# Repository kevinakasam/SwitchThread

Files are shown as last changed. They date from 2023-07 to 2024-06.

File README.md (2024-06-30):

# SwitchThread

The SwitchThread is a smol version of the [Voron Switchwire](https://github.com/VoronDesign/Voron-Switchwire). The goal of this project was/is to keep it in the *rules* of the [Printer for Ants](https://3dprintersforants.com/) - this means 1515 extrusions, a 120mm³ build volume, MGN 7H on all axis, Mini Stealthburner and so on.



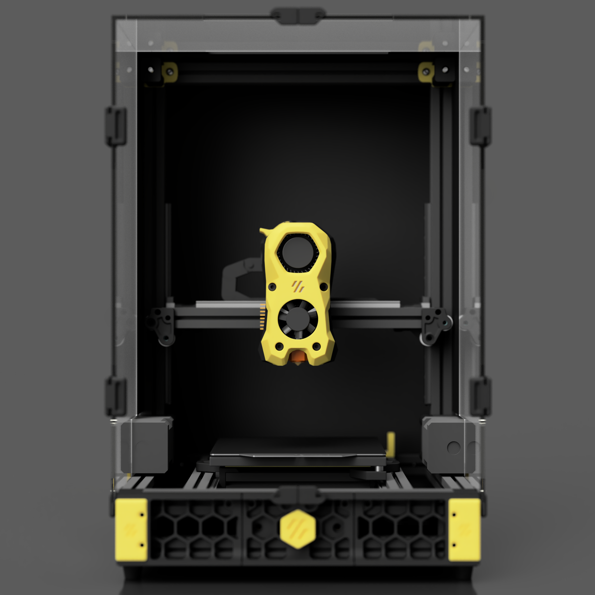
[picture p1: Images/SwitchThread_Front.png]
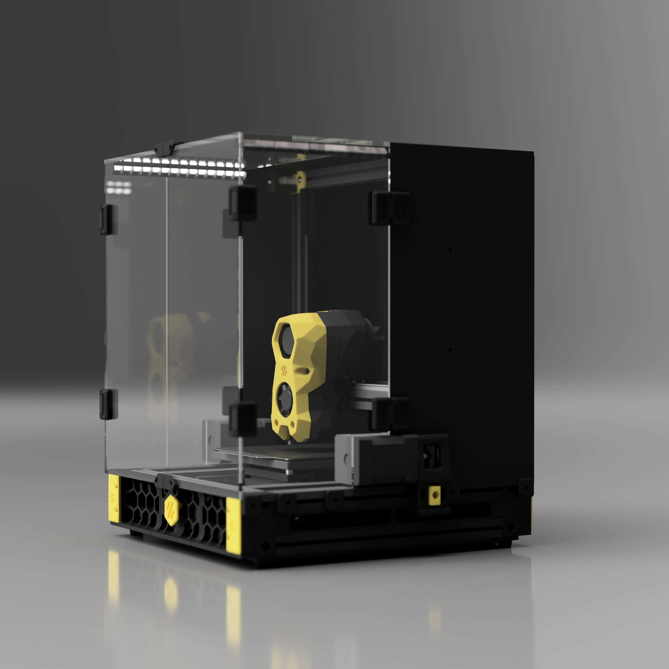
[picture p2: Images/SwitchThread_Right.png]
   

### Beta - Work in progress!

This is a very early work in progress. If you start building, you risk reprinting parts or spending money on hardware that will not be used in the final design. Please take a look at the SwitchThread channel on the [Doomcube Discord](https://discord.gg/doomcube).

The XZ gantry will be getting an update soon. I'm not a fan of the XZ tension mechanism, so I'll be customizing that part. So I would recommend waiting to print the XZ Gantry parts.

### Credits

- The printer is based on the [Voron Switchwire](https://github.com/VoronDesign/Voron-Switchwire) designed by the awesome [Voron Team](https://github.com/VoronDesign). Thanks for making this open source and allow fun projects like this!
- Also many thanks to the [Printer for Ants Team](https://www.3dprintersforants.com/) and Doomcube members for giving me chance to participate to project.
- And very special thanks to Schlongky for pushing me to finally start this project. Thanks for SwitchThreads name, your ideas and all the help with sourcing parts. Also thanks to Oldcrazy and Kyle for jumping on this project even though the CAD wasn't even finished yet!

### See it in action

SwitchThread by myself        |  SwitchThread by SchlongkyDong  
:-------------------------:|:-------------------------:
Serial Request (https://www.reddit.com/r/voroncorexy/comments/16sjrmx/serial_request_switchwire_switchthread_discord/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) | Serial Reques (https://www.reddit.com/r/voroncorexy/comments/16sk4o1/serial_request_switchwire_switchthread_discord/)

### BOM?

The SwitchThread is pretty much a V0 in a different shape, so with a V0 kit you will cover 99% of the parts you need. We're working on a more detailed BOM, but so far you should be fine with a few extra meters of belts and one or two extra pulleys (depending on the Y setup you want to use).

- GT2 Open Belt 6mm: V0 BOM calls for 3 Meters and I used exactly 3 Meters with dual Y, but then you shouldn't misscut
- F623-RS Bearing: V0 BOM calls for 24. You will need 22 with single Y and 28 with dual Y
- Frame: Setting a V0 Frame + a 100mm Tophat Kit as default you get everything you need to build the SwitchThread Frame. The SwitchThread has 300mm long Z extrusions, by deafult you're supposted to join a 200mm extrusion with a 100mm tophat extrusion (two times). Two more 100mm profiles are needed for the bed (so you need 4 100mm extrusions in total, 2 for the bed and 2 to raise z). This beeing said, the following scenarios are possible and should help you to understand what you need:
    - V0 Frame + 100mm Tophat Kit: Join a 200mm extrusion with one of the 100mm tophat extrusions - works perfectly fine with a M3 threaded rod or a headless M3 screw (Take a look [here](https://github.com/zruncho3d/BoxZero#frame))
    - V0 Frame + new 300mm profile: Rather than joining two extrusions together you can also get a new 300mm z extrusion. Probably the easiest way, requires more parts and money though
    - V0 Frame + a saw: If you only have a V0 Frame, you can use a saw to solve this. The SwitchThread will give you 1 spare 200mm profile - you can cut that in half to get the extra 100mm profile (remember you need 4 in total). I would use the cut profile on the bed, simply because it doesn't matter if your cut isn't 100% straight but it does for z.
- Boop: If you want to use Boop, the bed springs are a nogo, I will add a link to nylonspacers once Boop is confirmed.

### Boop and Dual Y

I try to keep this short: You have to decide if you want to use a single or dual Y Motor setup and if you want to use Boop or not. Alternatively you can also use an [ADXL Probe](https://github.com/jniebuhr/adxl345-probe) or any other bed probe - I also want to implement [Klicky](https://github.com/jlas1/Klicky-Probe) + [Sexbolt](https://github.com/VoronDesign/VoronUsers/tree/master/printer_mods/hartk1213/Voron2.4_SexBolt_ZEndstop) to use the [Automatic Z-Calibration](https://github.com/protoloft/klipper_z_calibration#moonraker-updater) macro - I assume we will need a longer x rail for that though, I can't tell right now.

#### Boop

The goal is to support [Boop](https://github.com/PrintersForAnts/Boop) - a mini version of the [Voron Tap](https://github.com/VoronDesign/Voron-Tap/). This hasnt been tested yet but I tried my best to make the Bed as rigid as possible - we will see if that works out. However the decision if you want to use Boop or not is important for the frame build. If you*re going to use boop, you can reuse the counterbore holes in the E-Extrusions of the V0 Frame. If you don't want to use Boop, you will have to drill your own holes.

#### Single / Dual Y

Since we use a 120mm casted bed, there's quite some mass to move around. We had the idea to squeeze to Y motors in there to double the power. This means that you will need an extra Nema 14 stepper (not a driver, you can use the parallel z port on most Mobos) and some extra belts + bearings  (see BOM section above). Also the LRS150 wouldn't fir under the printer - I will find a solution for that.

### ChangeLog

30.06.2024
- Well, finally the first real push of all files. Everything aside panels is working and ready to print :D

28.09.2023
- Mostly bug fixes
- Added missing STLs, everything should be tested now

01.08.2023: XZ Update
- Fixed an issue with the belt path on the right idler
- Added Alternative XZ Tensioners, these will require some different hardware, main difference is a M3x40mm screw and a F623 bearing per side

28.07.2023: Initial Upload

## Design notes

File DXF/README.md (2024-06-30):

Panels are still in the dev. Please use the CAD to take a look at the current state. Aside the Mid panels, everything should fit. Please ping me on Discord before buying any panels.

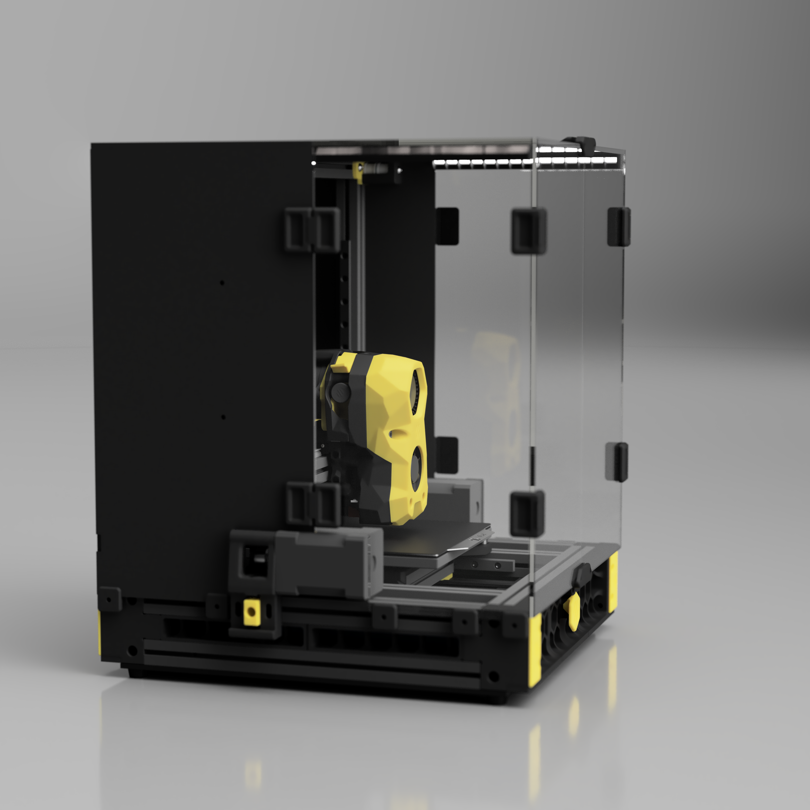
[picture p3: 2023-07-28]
Images/SwitchThread_Left.png

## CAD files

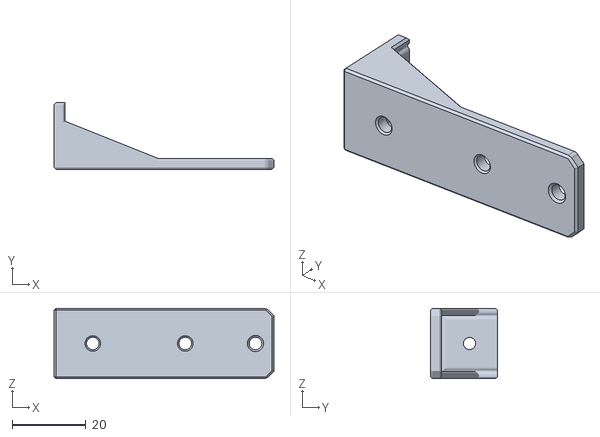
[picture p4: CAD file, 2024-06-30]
STLs/DrillGuide.stl
59.5 x 18.0 x 19.0

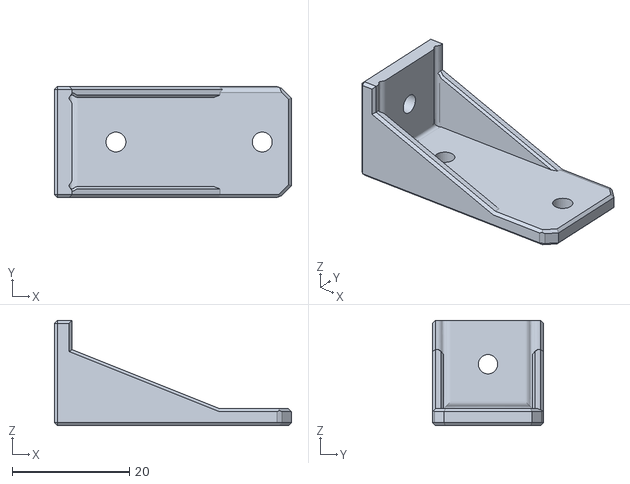
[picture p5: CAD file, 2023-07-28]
STLs/Gantry/DrillGuide.stl
40.5 x 19.0 x 18.0

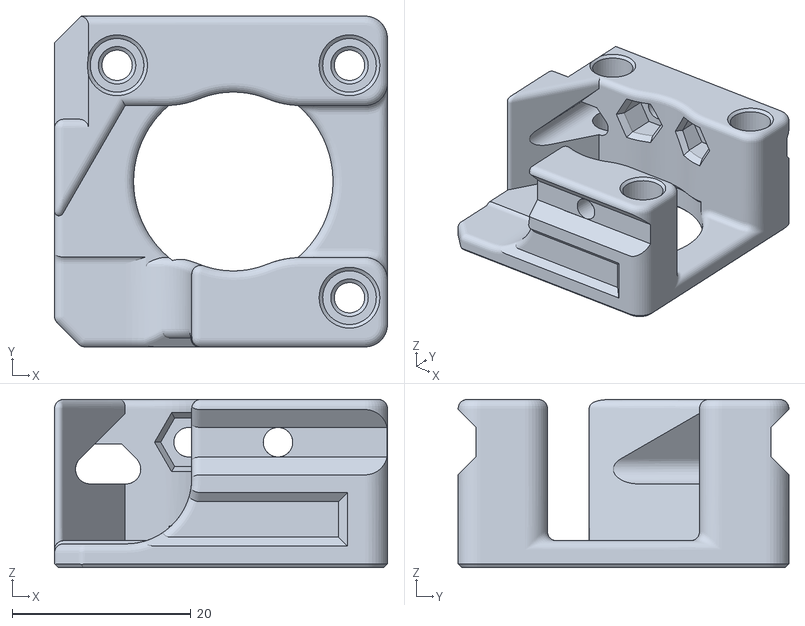
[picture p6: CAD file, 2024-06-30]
STLs/Gantry/XZ_Axis/Alternative_Drive_Frame/[a]_z_motor_tensioner.stl
37.3 x 37.0 x 18.8

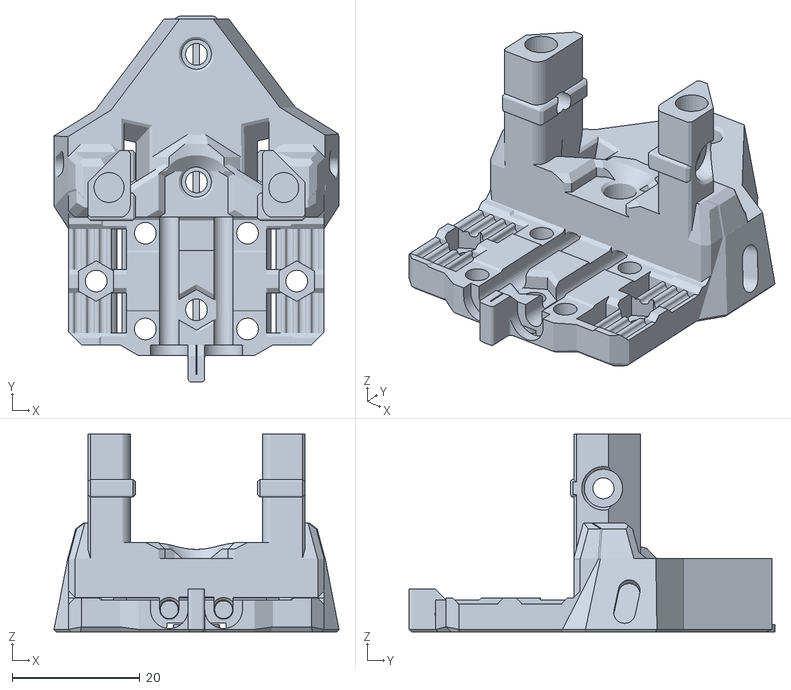
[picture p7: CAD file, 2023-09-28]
STLs/Gantry/XZ_Axis/X_Carriage/Boop/[a]_boop_center_optical.stl
44.6 x 57.3 x 31.0

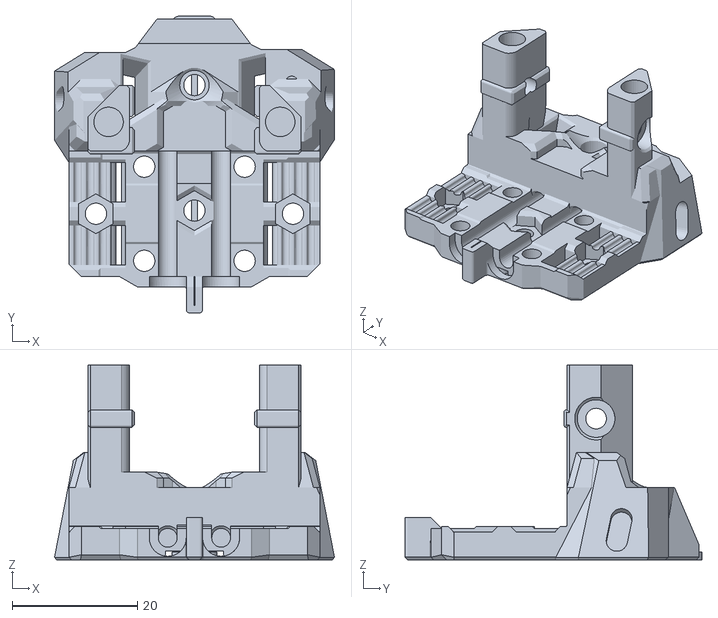
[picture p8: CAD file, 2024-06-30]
STLs/Gantry/XZ_Axis/X_Carriage/Boop/BabyBoop/[a]_boop_center_optical_40mm.stl
44.6 x 47.3 x 31.0

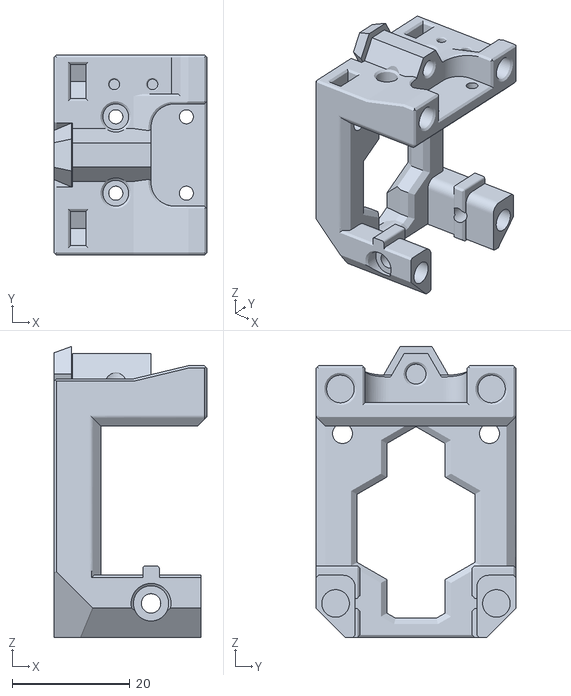
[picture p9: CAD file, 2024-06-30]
STLs/Gantry/XZ_Axis/X_Carriage/X_Carriage_a_endstop.stl
26.0 x 34.0 x 49.5

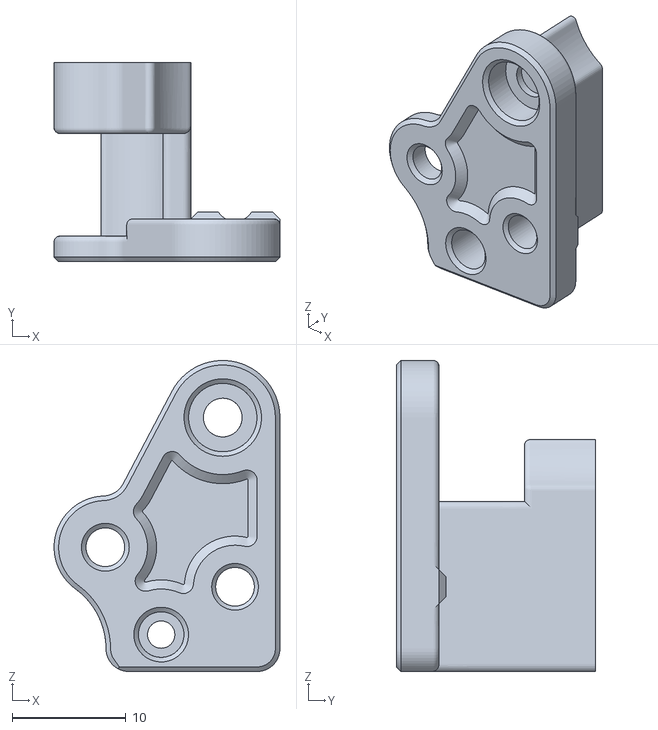
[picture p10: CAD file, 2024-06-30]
STLs/Gantry/XZ_Axis/xz_block_right.stl
19.8 x 17.5 x 27.3

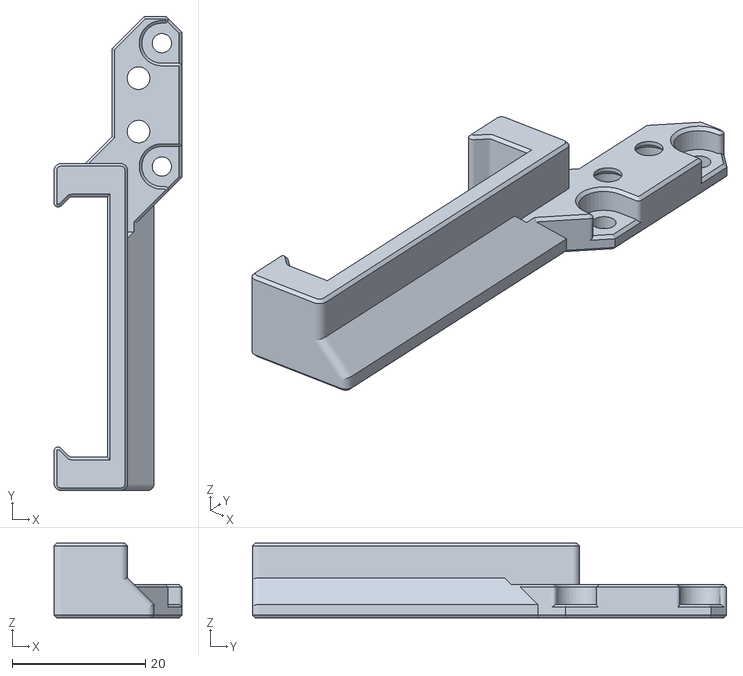
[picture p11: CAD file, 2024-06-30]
STLs/Gantry/Y_Axis/[a]_y_chain_bed_mount_generic_brush.stl
19.2 x 71.0 x 11.2

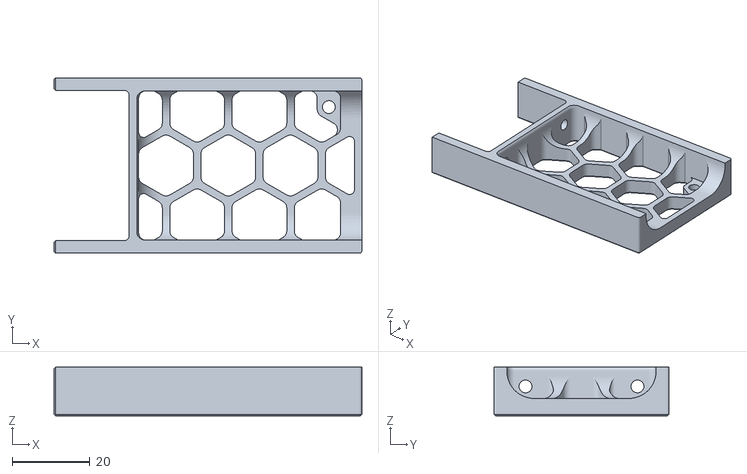
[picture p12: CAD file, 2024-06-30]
STLs/Skirts/grill_A_x2.stl
79.0 x 45.0 x 12.5

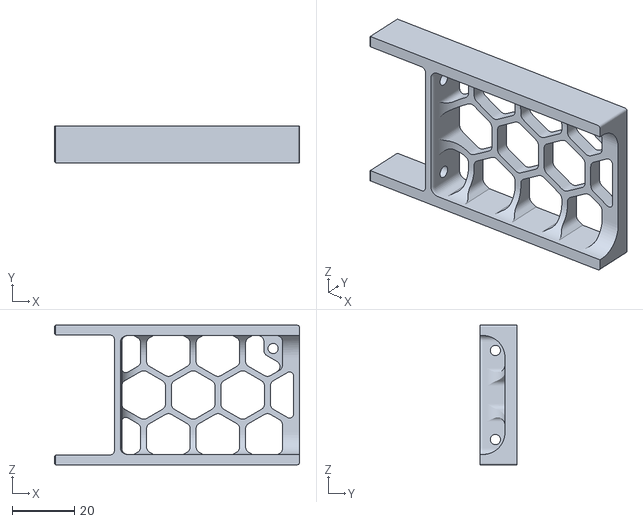
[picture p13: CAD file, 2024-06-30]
STLs/Skirts/Mesh_Skirts/grill_A_mesh_x2.stl
79.0 x 11.9 x 45.0

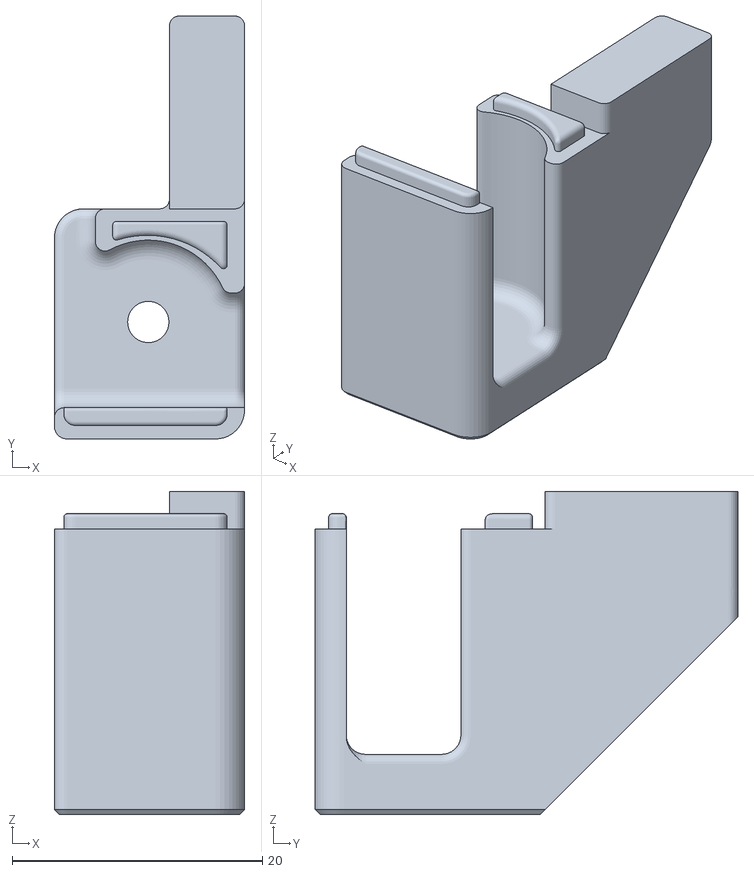
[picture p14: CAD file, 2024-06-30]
STLs/Gantry/XZ_Axis/upper_idler_support_a_left.stl
15.2 x 33.8 x 25.8

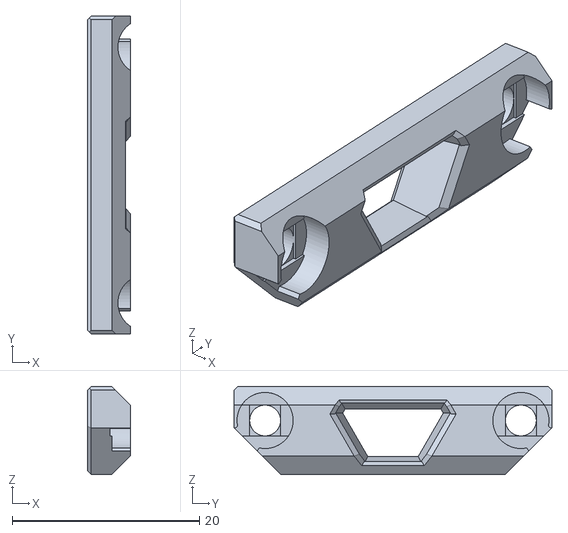
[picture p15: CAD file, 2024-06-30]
STLs/Gantry/XZ_Axis/X_Carriage/X_Carriage_b.stl
4.60 x 34.0 x 9.45

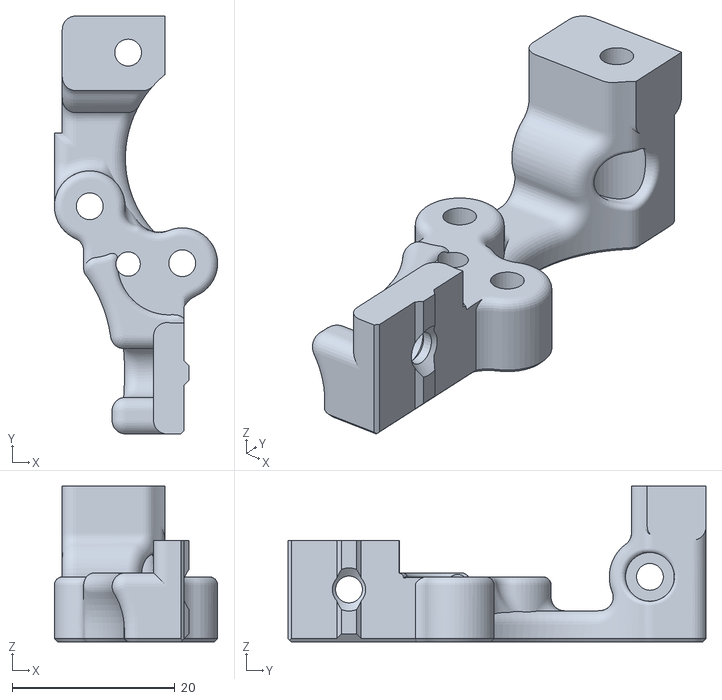
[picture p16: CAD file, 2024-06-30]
STLs/Gantry/Y_Axis/y_motor_mount_a.stl
20.1 x 51.4 x 19.2

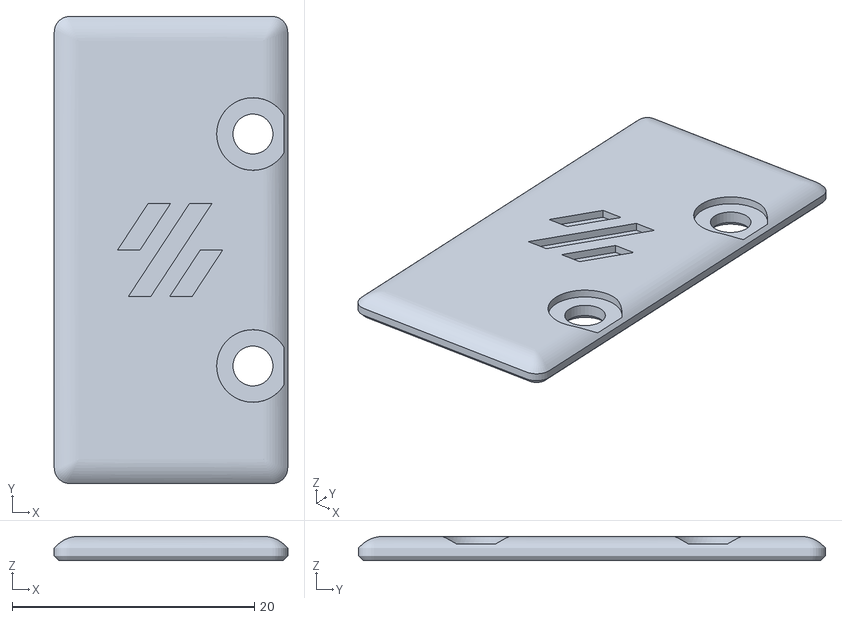
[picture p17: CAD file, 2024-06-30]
STLs/Skirts/[a]_grill_endcap_x4.stl
19.3 x 38.6 x 2.00

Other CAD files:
STLs/Gantry/XZ_Axis/Alternative_Drive_Frame/[a]_x_motor_tensioner.stl
STLs/Skirts/Mesh_Skirts/front_mid_grill_x1.stl
STLs/Gantry/XZ_Axis/Alternative_Drive_Frame/z_motor_frame.stl
STLs/Gantry/XZ_Axis/X_Carriage/X_Carriage_a.stl
STLs/Gantry/XZ_Axis/Alternative_Drive_Frame/[a]_tensioner_wedge_x2.stl
STLs/Gantry/XZ_Axis/Alternative_Drive_Frame/x_motor_frame.stl
STLs/Gantry/XZ_Axis/X_Carriage/[a]_xz_belt_clip_x2.stl
STLs/Gantry/XZ_Axis/[a]_upper_idler_support_b_left.stl
STLs/Gantry/XZ_Axis/[a]_upper_idler_support_b_right.stl
STLs/Gantry/XZ_Axis/[a]_x_endstop_mount.stl
STLs/Gantry/XZ_Axis/[a]_xz_tensioner_x2.stl
STLs/Gantry/XZ_Axis/[a]_z_endstop_mount.stl
STLs/Gantry/XZ_Axis/upper_idler_support_a_right.stl
STLs/Gantry/XZ_Axis/x_motor_mount_a.stl
STLs/Gantry/XZ_Axis/x_motor_mount_b.stl
STLs/Gantry/XZ_Axis/xz_block_left.stl
STLs/Gantry/XZ_Axis/z_bearing_block_left.stl
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

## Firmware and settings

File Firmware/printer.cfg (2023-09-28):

## *** THINGS TO CHANGE/CHECK: ***
## MCU paths                         	[mcu] section
## Thermistor types                      [extruder] and [heater_bed] sections - See 'sensor types' list at end of file
## PID tune                              [extruder] and [heater_bed] sections
## Fine tune E steps                     [extruder] section

## For wiring directions please see https://docs.vorondesign.com/build/electrical/sw_miniE3_v20_wiring.html

## Webclient config files. Uncomment one depending on UI being used.
[include mainsail.cfg]
#[include fluidd.cfg] 
[include ebb.cfg]
[include startend.cfg]
[include filament.cfg]

[printer]
kinematics: corexz
max_velocity: 200
max_accel: 1000
max_z_velocity: 50
max_z_accel: 1000
square_corner_velocity: 4.0

[mcu]
###Change to device found by "ls -l /dev/serial/by-id/" with just one this MCU connected to Pi
serial: /dev/ttyAMA0
restart_method: command

#####################################################################
# 	X Stepper Settings
#####################################################################

######
# Motor -XM
# Endstop - X-STOP
###############
[stepper_x]
step_pin: gpio11
dir_pin: gpio10
enable_pin: !gpio12
microsteps: 32
rotation_distance: 40
#endstop_pin: ^gpio4
endstop_pin: tmc2209_stepper_x:virtual_endstop
# homing_retract_dist: 0
position_endstop: 120
position_max: 120
homing_speed: 20
homing_positive_dir: true

[tmc2209 stepper_x]
uart_pin: gpio9
tx_pin: gpio8
uart_address: 0
run_current: 0.4
#hold_current: 0.3
interpolate: False
stealthchop_threshold: 0
diag_pin: ^gpio4
driver_SGTHRS: 50

#####################################################################
#   Y Stepper Settings
#####################################################################

######
# Motor -ZM
# Endstop - Z-STOP
###############
[stepper_y]
step_pin: gpio19
dir_pin: gpio28
enable_pin: !gpio2
microsteps: 16
rotation_distance: 40
#endstop_pin: ^gpio3
endstop_pin: tmc2209_stepper_y:virtual_endstop
# homing_retract_dist: 0
position_endstop: 120
position_max: 120
homing_speed: 20
homing_positive_dir: true

[tmc2209 stepper_y]
uart_pin: gpio9
tx_pin: gpio8
uart_address: 1
run_current: 0.8 #Dual Y = 2x current
#hold_current: 0.3
interpolate: False
stealthchop_threshold: 0
diag_pin: ^gpio25
driver_SGTHRS: 62

#####################################################################
# 	Z Stepper Settings
#####################################################################

######
# Motor -YM
# Endstop - Y-STOP
###############
[stepper_z]
step_pin: gpio6
dir_pin: gpio5
enable_pin: !gpio7
microsteps: 16
rotation_distance: 40
full_steps_per_rotation: 200
endstop_pin: ^gpio16
#position_endstop: 120
position_max: 120
homing_speed: 10
position_min: -3.0

[tmc2209 stepper_z]
uart_pin: gpio9
tx_pin: gpio8
uart_address: 2
run_current: 0.4
#hold_current: 0.3
interpolate: False
stealthchop_threshold: 0

#####################################################################
# 	Bed Heater
#####################################################################

######
# BED Connector
###############
[heater_bed]
heater_pin: gpio21
sensor_type: NTC 100K MGB18-104F39050L32
sensor_pin: gpio26
min_temp: -200
max_temp: 120
control: pid
pid_Kp:64.510
pid_Ki:1.911
pid_Kd:544.300

#####################################################################
# 	Probe
#####################################################################

######
#Z Max Connector on Z(main) Board
#Inductive Probe
###############
#[probe]
##      If your probe is NO instead of NC, add change pin to !z:P1.24
#pin: ^PC2
#x_offset: 0
#y_offset: 25
#z_offset: 0
#samples: 3
#samples_result: median
#sample_retract_dist: 3
#samples_tolerance: 0.006
#samples_tolerance_retries: 3

#####################################################################
# 	Fan Control
#####################################################################

######
# Electronics Fan
# FAN1 Connector
###############
[controller_fan my_controller_fan]
pin: gpio20
max_power: 1.00
kick_start_time: 0.200
heater: heater_bed

#####################################################################
#   Homing and Bed Mesh
#####################################################################
[homing_override]
axes: xyz
set_position_z: 0
gcode:
  {% set home_all = 'X' not in params and 'Y' not in params and 'Z' not in params %}

  G90
  G0 Z5
  G4 P1000 # Wait just a second… (give StallGuard registers time to clear)

  {% if home_all or 'X' in params %}
    _HOME_X
  {% endif %}

  {% if home_all or 'Y' in params %}
    _HOME_Y
  {% endif %}
  
  {% if home_all or 'Z' in params %}
    G90
    #G0 X120 Y100 Z10 F9000
    G28 Z0
    G0 Z30 
  {% endif %}
  
# Macros

[gcode_macro _HOME_X]
gcode:
    G4 P1000     # Wait just a second… (give StallGuard registers time to clear)
    # Always use consistent run_current on A/B steppers during sensorless homing
    {% set RUN_CURRENT_X = printer.configfile.settings['tmc2209 stepper_x'].run_current|float %}
    {% set RUN_CURRENT_Z = printer.configfile.settings['tmc2209 stepper_z'].run_current|float %}
    {% set HOME_CURRENT_RATIO = 0.7 %} # by default we are dropping the motor current during homing. you can adjust this value if you are having trouble with skipping while homing
    SET_TMC_CURRENT STEPPER=stepper_x CURRENT={HOME_CURRENT_RATIO * RUN_CURRENT_X}
    SET_TMC_CURRENT STEPPER=stepper_z CURRENT={HOME_CURRENT_RATIO * RUN_CURRENT_Z}

    # Home
    G28 X
    # Move away
    #G91
    #G1 X-10 F1200
    G4 P1000 # Wait just a second… (give StallGuard registers time to clear)
    # Set current during print
    SET_TMC_CURRENT STEPPER=stepper_x CURRENT={RUN_CURRENT_X}
    SET_TMC_CURRENT STEPPER=stepper_z CURRENT={RUN_CURRENT_Z}

[gcode_macro _HOME_Y]
gcode:
    # Set current for sensorless homing
    # Always use consistent run_current on A/B steppers during sensorless homing
    {% set RUN_CURRENT_Y = printer.configfile.settings['tmc2209 stepper_y'].run_current|float %}
    {% set HOME_CURRENT_RATIO = 0.7 %} # by default we are dropping the motor current during homing. you can adjust this value if you are having trouble with skipping while homing
    SET_TMC_CURRENT STEPPER=stepper_y CURRENT={HOME_CURRENT_RATIO * RUN_CURRENT_Y}

    # Home
    G28 Y
    # Move away
    #G91
    #G1 Y-10 F1200

    # Set current during print
    SET_TMC_CURRENT STEPPER=stepper_y CURRENT={RUN_CURRENT_Y}

#[homing_override]
#axes: z
#set_position_z: 0
#gcode:
#    G90
#    G0 Z5 F500
#    G28 X0 Y0
#    G0 X125 Y100 F9000
#    G28 Z0
#    G0 Z5 F500

#[bed_mesh]
#speed: 150
#horizontal_move_z: 5
#mesh_min: 
#mesh_max: 
#probe_count: 6,6
#algorithm: bicubic
#fade_start: 1
#fade_end: 10
#fade_target: 0

#####################################################################
# 	Displays
#####################################################################
## 	For the mini12864 Display, the [display] and [neopixel] must be uncommented
# mini12864 LCD Display
# connected to exp1/2
#[display]
##    mini12864 LCD Display
#lcd_type: uc1701
#cs_pin: PB8
#a0_pin: PB15
#rst_pin: PB9
#encoder_pins: ^PA9,^PA10
#click_pin: ^!PB5
#contrast: 63
#spi_software_sclk_pin: PA5
#spi_software_mosi_pin: PA7
#spi_software_miso_pin: PA6
#menu_reverse_navigation: True

#[neopixel fysetc_mini12864]
##	To control Neopixel RGB in mini12864 display
## Remember with these ones, you'll need to remove the connector header on the LCD for EXT1 + 2
## (it slides off) and reverse it for it to work on your SKR (1.3 and 1.4) board
#pin: PA15
#chain_count: 3
#initial_RED: 1
#initial_GREEN: 1
#initial_BLUE: 1
#color_order: RGB

##	Set RGB values on boot up for each Neopixel. 
##	Index 1 = display, Index 2 and 3 = Knob
#[delayed_gcode setdisplayneopixel]
#initial_duration: 1
#gcode:
#        SET_LED LED=fysetc_mini12864 RED=1 GREEN=1 BLUE=1 INDEX=1 TRANSMIT=0	# Backlit Screen colour
#        SET_LED LED=fysetc_mini12864 RED=1 GREEN=0 BLUE=0 INDEX=2 TRANSMIT=0	# Top left Knob colour
#        SET_LED LED=fysetc_mini12864 RED=1 GREEN=0 BLUE=0 INDEX=3				# Bottom right knob colour

#####################################################################
#   Case Lights
#####################################################################
[output_pin LIGHTS]
pin: gpio24
value: 0
shutdown_value: 0

[gcode_macro lights_on]
gcode:
    SET_PIN PIN=LIGHTS VALUE=1.0

[gcode_macro lights_off]
gcode:
    SET_PIN PIN=LIGHTS VALUE=0.0



#*# <---------------------- SAVE_CONFIG ---------------------->
#*# DO NOT EDIT THIS BLOCK OR BELOW. The contents are auto-generated.
#*#
#*# [stepper_z]
#*# position_endstop = 118.175

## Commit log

2023-07-28 Initial Upload
    [DrillGuide.stl, Feet_A_x2.stl, Feet_B_x2.stl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]
2023-08-01 XZ Update
    [[a]_tensioner_wedge_x2.stl, [a]_x_motor_tensioner.stl, [a]_z_motor_tensioner.stl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]
2023-09-28 STL Update
    [Deck Panel.stl, Door_Hinge_x4.stl, DrillGuide.stl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]
2024-06-30 Full Export
    [Deck Panel.stl, Door_Hinge_x4.stl, DrillGuide.stl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]
